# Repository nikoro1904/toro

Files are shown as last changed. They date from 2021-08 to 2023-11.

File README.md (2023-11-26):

# TORO

TORO is the name of my **T**ennis b**O**ll **RO**bot.

2023:
toro_112023
2021:
toro_082021

Some day in the future, TORO should be able to drive and navigate on a tennis court, search for tennis bolls, approach them, pick them up and eventually bring them back to me. It would also be nice to make TORO in a more generalistic matter so it can adapt or be adapted to different kind of bolls (such as golf bolls for example).

This repo contains general notes, electronic circuits, 3D parts and code of TORO. It is nowhere near being finished but will hopefully be some day. When this is the case, I might upload more detailed instructions on how to built TORO.

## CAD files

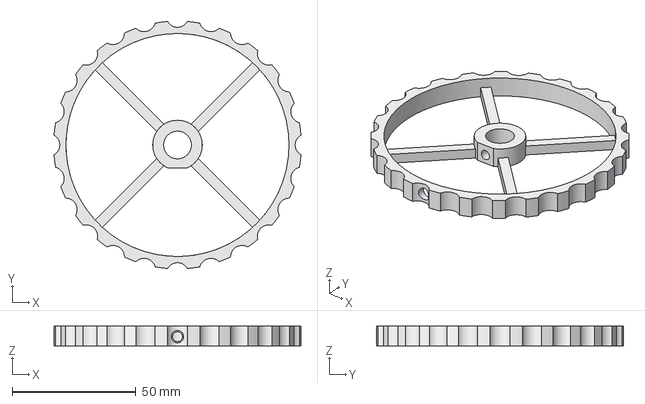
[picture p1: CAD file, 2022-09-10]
3d_parts/Rad_ringeinsatz.FCStd
99.7 x 99.7 x 8.00 mm

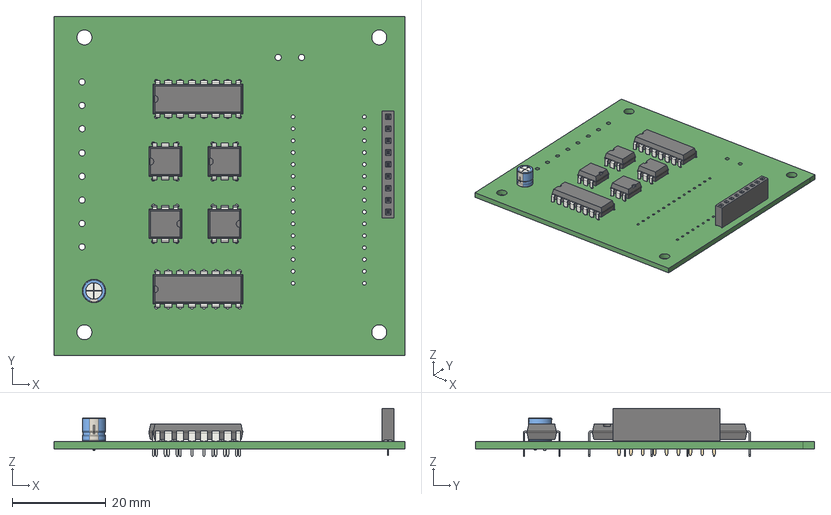
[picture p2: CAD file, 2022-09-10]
circuits/Toro_Stepper_Differential_Rev3/Toro_Stepper_Differential.step
75.0 x 72.5 x 10.3 mm

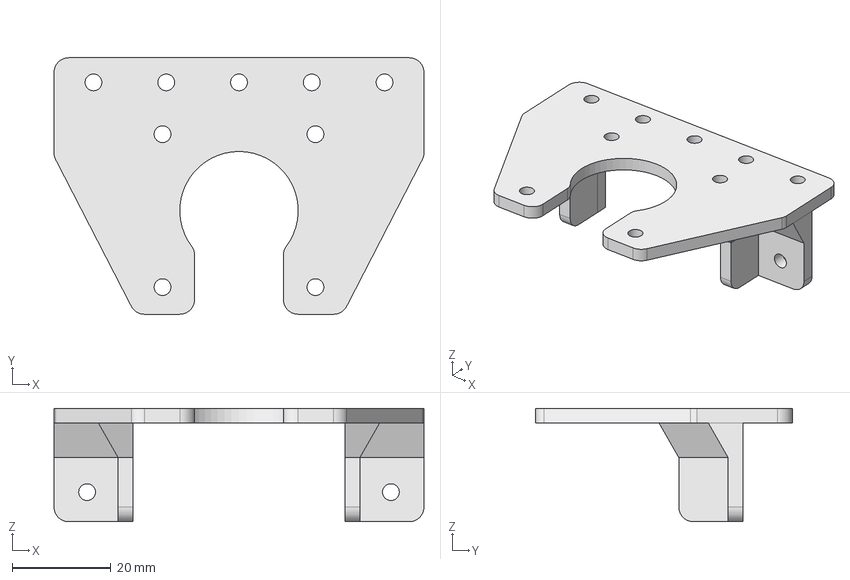
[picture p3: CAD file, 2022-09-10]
3d_parts/stepper_abdeckung.FCStd
75.0 x 52.0 x 23.0 mm

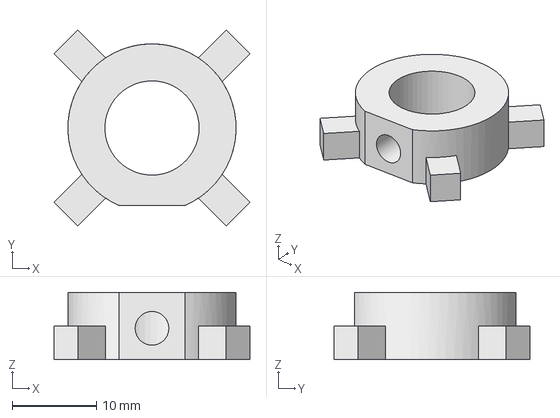
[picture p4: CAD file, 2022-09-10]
3d_parts/Rad_dummy_ringeinsatz.FCStd
23.3 x 23.3 x 8.00 mm

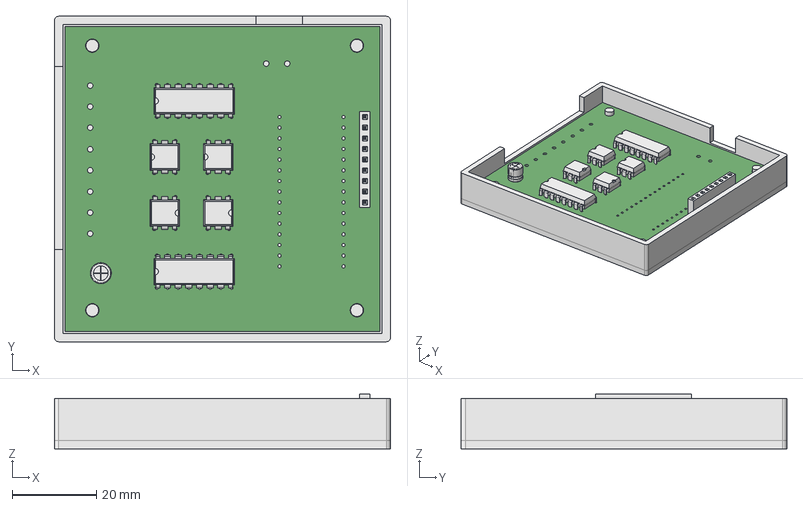
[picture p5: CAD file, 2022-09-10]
3d_parts/motor_platine_box.FCStd
80.0 x 77.5 x 13.1 mm

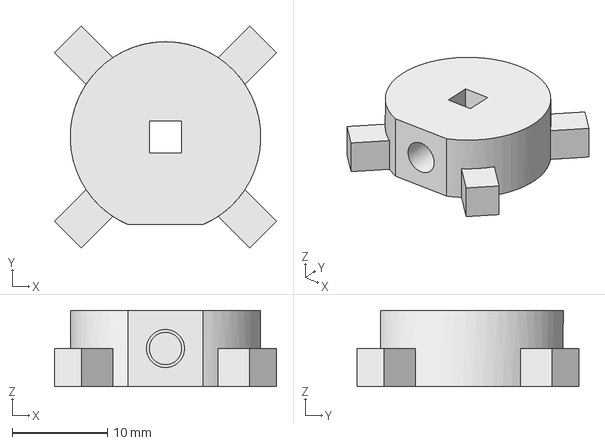
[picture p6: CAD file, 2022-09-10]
3d_parts/Rad_dummy_gewindeeinsatz.FCStd
23.3 x 23.3 x 8.00 mm

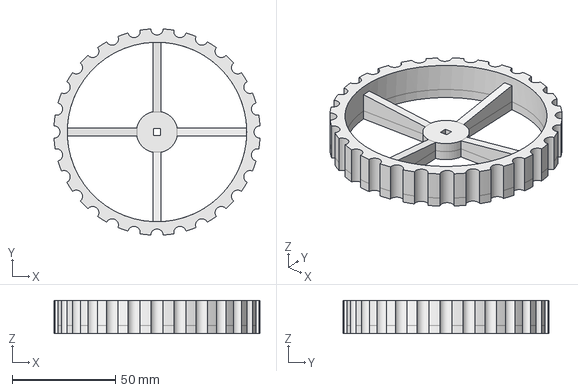
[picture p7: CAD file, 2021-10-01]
3d_parts/rad_breit_3,4.FCStd
99.8 x 99.8 x 16.0 mm

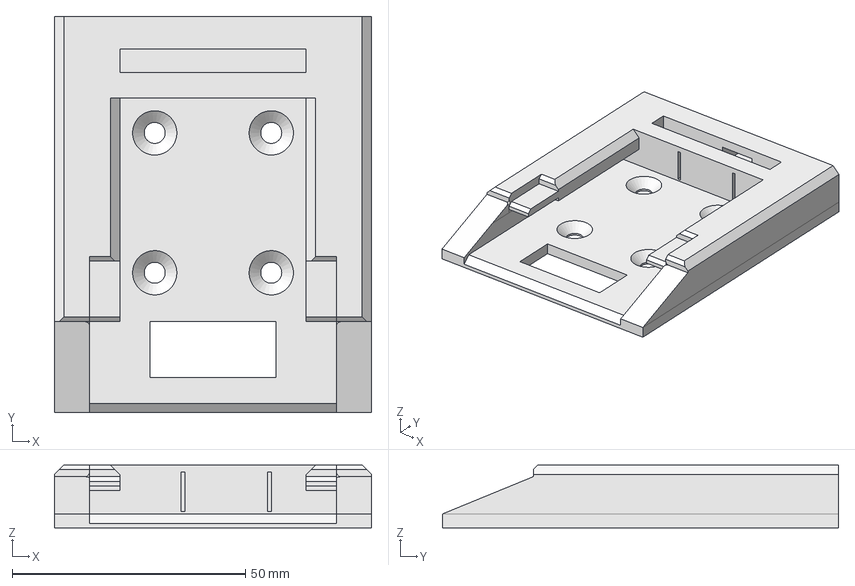
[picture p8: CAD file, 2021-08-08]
3d_parts/Akku_Aufnahme.FCStd
68.0 x 85.0 x 13.5 mm

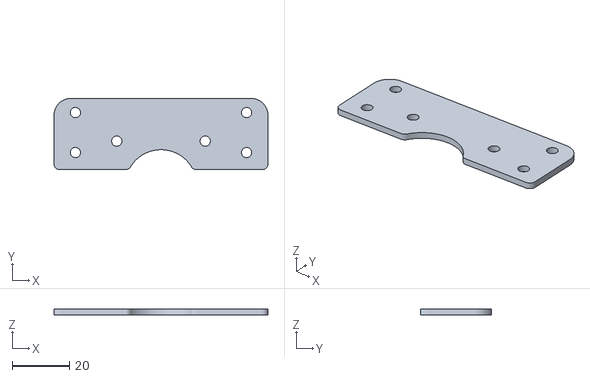
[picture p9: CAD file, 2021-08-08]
3d_parts/abdeckung_stepper_v2.stl
75.0 x 25.0 x 2.00

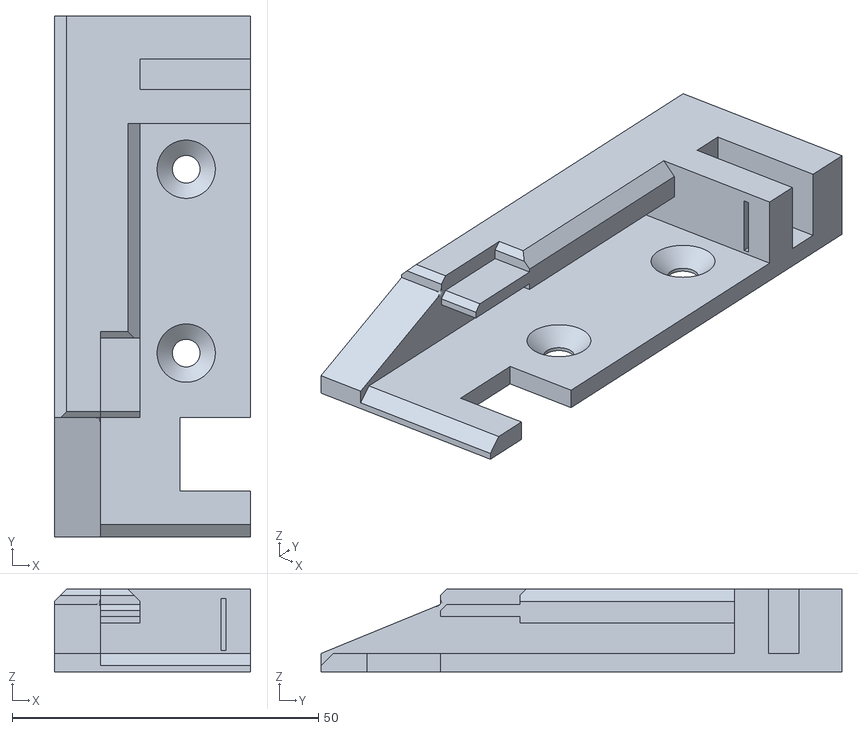
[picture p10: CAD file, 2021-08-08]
3d_parts/AA_kurz_v3.stl
32.0 x 85.0 x 13.5

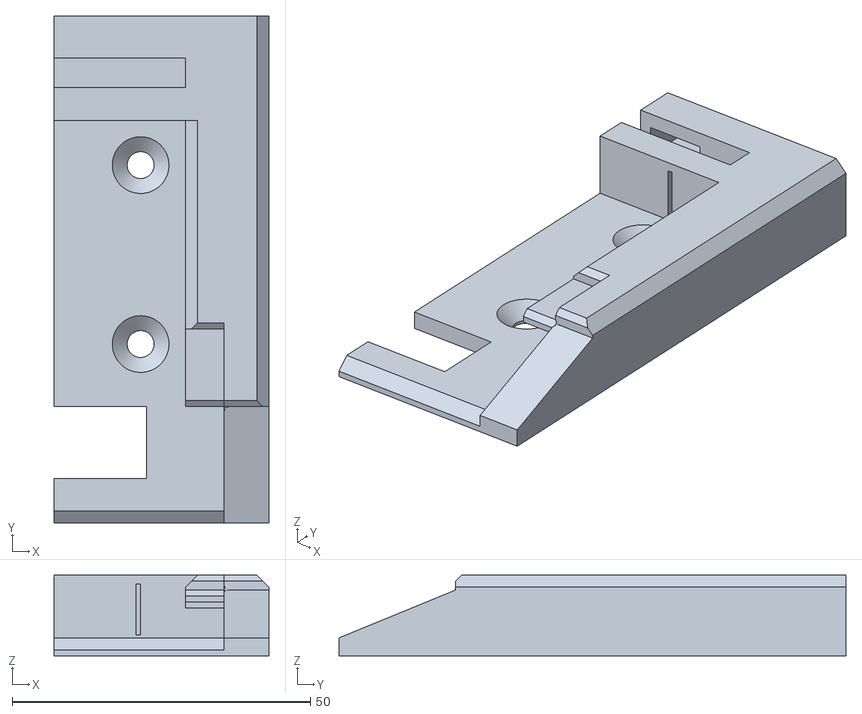
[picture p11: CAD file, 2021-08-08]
3d_parts/AA_lang_v3.stl
36.0 x 85.0 x 13.5

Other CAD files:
3d_parts/rad_komplett_3,4.FCStd
3d_parts/Rad_dummy_gewindeeinsatz.stl
3d_parts/Rad_ringeinsatz.stl
3d_parts/motor_platine_box.stl
3d_parts/rad_breit_3,4.stl
3d_parts/rad_komplett_3,4.stl

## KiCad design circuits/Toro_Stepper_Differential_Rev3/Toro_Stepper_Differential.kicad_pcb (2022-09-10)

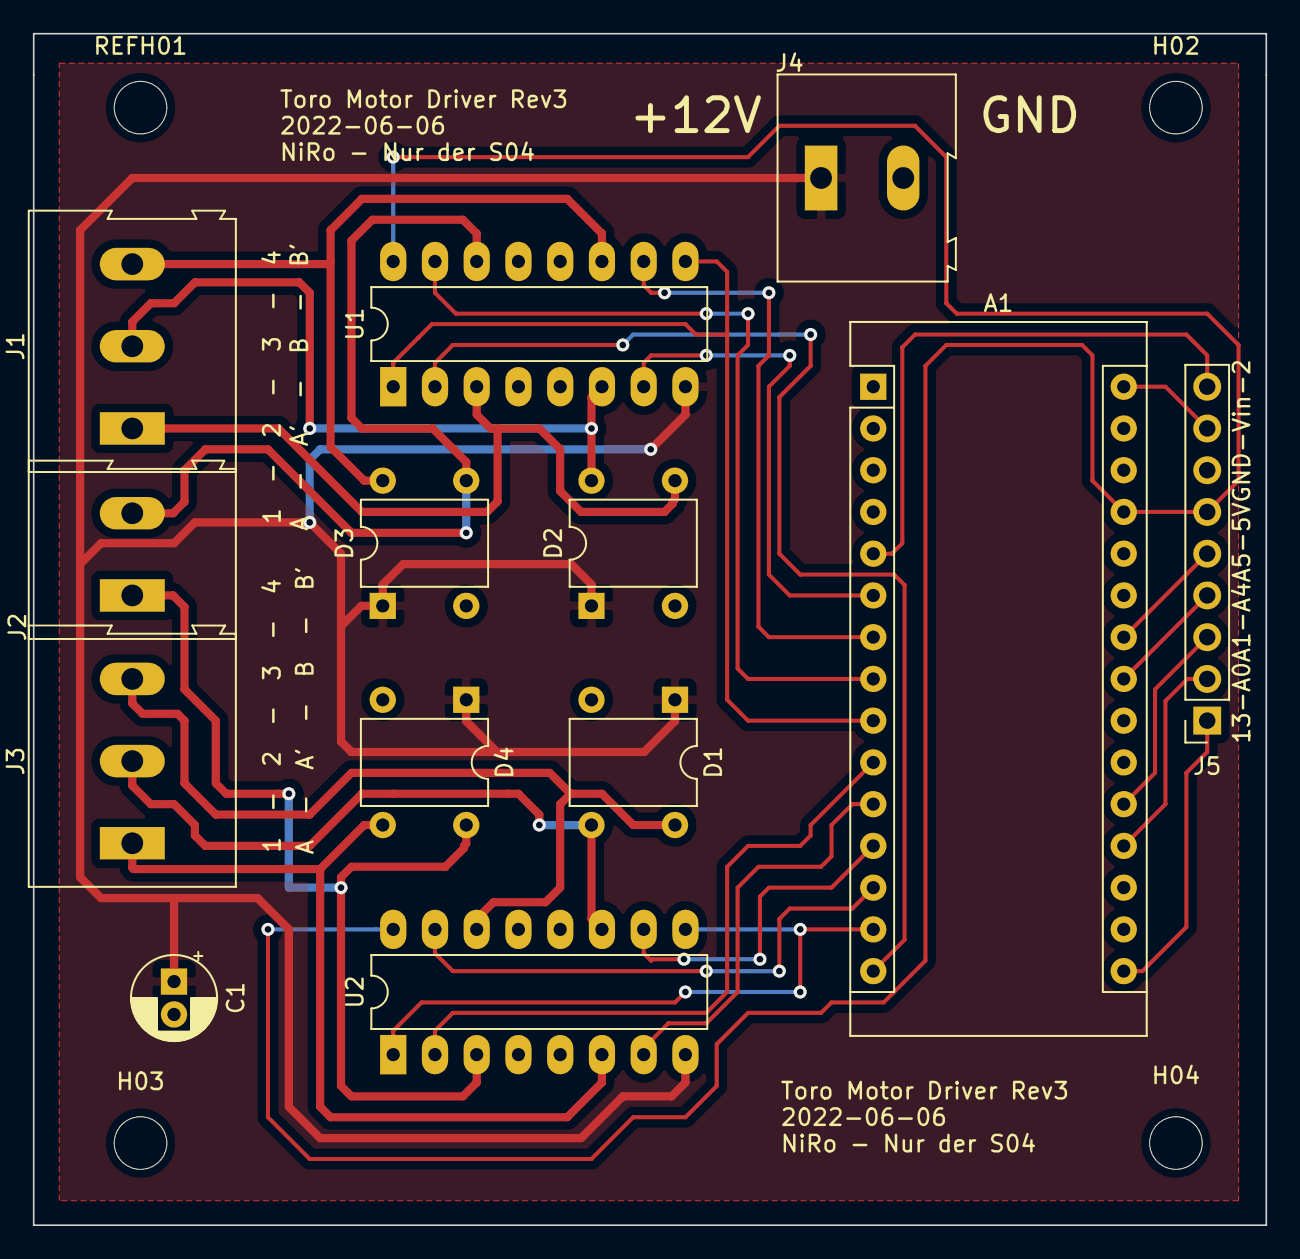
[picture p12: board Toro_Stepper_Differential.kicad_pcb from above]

Board: 2 copper layers, 75.0 x 72.5 mm, 17 parts (0 on the bottom side), 28 nets.

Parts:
A1: Arduino_Nano_v3.x; Arduino_Nano
C1: 220nF; CP_Radial_D5.0mm_P2.00mm
D1, D2, D3, D4: D_Bridge_+-AA; BridgeRectifier_+-AA
H02, H03, H04: MountingHole_3.2mm_M3_ISO14580
J1, J3: Screw_Terminal_01x03; TerminalBlock_Altech_AK300-3_P5.00mm
J2: Screw_Terminal_01x02; TerminalBlock_Altech_AK300-2_P5.00mm
J4: Screw_Terminal _01x02; TerminalBlock_Altech_AK300-2_P5.00mm
J5: Conn_01x09_Male; PinSocket_1x09_P2.54mm_Vertical
REFH01: MountingHole_3.2mm_M3_ISO14580
U1, U2: L293; DIP-16_W7.62mm_LongPads

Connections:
+10V: C1.1, D1.1, D2.1, D3.1, D4.1, J4.1, U1.8, U2.8
GND: A1.4, A1.29, C1.2, D1.2, D2.2, D3.2, D4.2, J4.2, J5.7, U1.4, U1.5, U1.12, U1.13, U2.4, U2.5, U2.12, U2.13
unnamed: A1.5, J5.9
unnamed: A1.6, U1.7
unnamed: A1.7, U1.10
unnamed: A1.8, U1.15
unnamed: A1.9, U1.1, U1.9
unnamed: A1.10, U2.2
unnamed: A1.11, U2.7
unnamed: A1.12, U2.10
unnamed: A1.13, U2.15
unnamed: A1.14, U2.1, U2.9
unnamed: A1.15, U1.2
unnamed: A1.16, J5.1
unnamed: A1.19, J5.2
unnamed: A1.20, J5.3
unnamed: A1.23, J5.4
unnamed: A1.24, J5.5
unnamed: A1.27, J5.6, U1.16, U2.16
unnamed: A1.30, J5.8
unnamed: D1.3, J3.2, U2.11
unnamed: D1.4, J3.3, U2.14
unnamed: D2.3, J1.1, U1.3
unnamed: D2.4, J1.2, U1.6
unnamed: D3.3, J2.2, U1.14
unnamed: D3.4, J1.3, U1.11
unnamed: D4.3, J3.1, U2.6
unnamed: D4.4, J2.1, U2.3

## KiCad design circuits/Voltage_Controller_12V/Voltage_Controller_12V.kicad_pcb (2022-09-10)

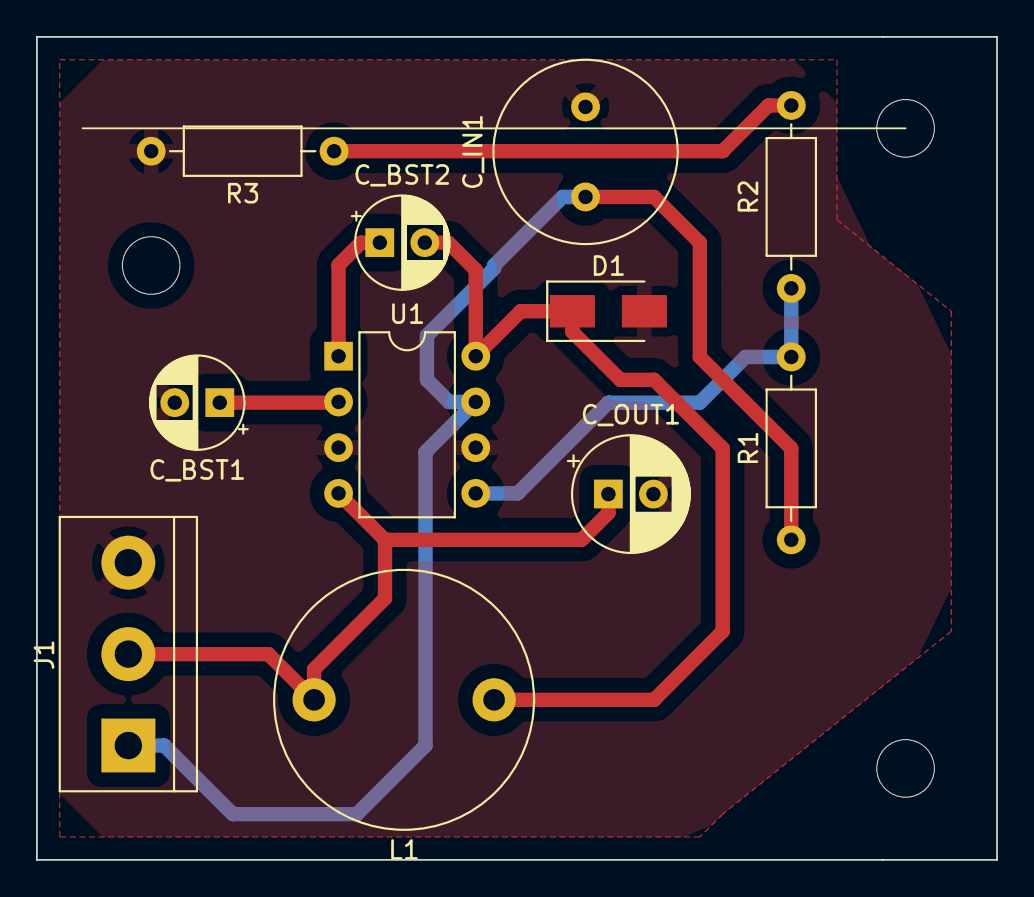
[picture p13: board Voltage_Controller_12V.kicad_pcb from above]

Board: 2 copper layers, 53.3 x 45.7 mm, 11 parts (0 on the bottom side), 8 nets.

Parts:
C_BST1, C_BST2: 0.1µF Tantal; CP_Radial_D5.0mm_P2.50mm
C_IN1: 220µF ELKO; C_Radial_D10.0mm_H16.0mm_P5.00mm
C_OUT1: 15µF Tantal; CP_Radial_D6.3mm_P2.50mm
D1: MBRA 340T3G ONS; D_SMA
J1: Screw_Terminal_01x03; TerminalBlock_bornier-3_P5.08mm
L1: 220µH; L_Radial_D14.2mm_P10.00mm_Neosid_SD14
R1: 1M; R_Axial_DIN0207_L6.3mm_D2.5mm_P10.16mm_Horizontal
R2: 100K; R_Axial_DIN0207_L6.3mm_D2.5mm_P10.16mm_Horizontal
R3: 47K; R_Axial_DIN0207_L6.3mm_D2.5mm_P10.16mm_Horizontal
U1: MAX5035CUPA; DIP-8_W7.62mm

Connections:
+12V: C_OUT1.1, J1.2, L1.2, U1.4
GND: C_BST1.2, C_IN1.2, C_OUT1.2, D1.2, J1.3, R3.2, U1.3, U1.6
unnamed: C_BST1.1, U1.2
unnamed: C_BST2.1, U1.1
unnamed: C_BST2.2, D1.1, L1.1, U1.8
unnamed: R1.2, R2.1, U1.5
unnamed: R2.2, R3.1
Vdrive: C_IN1.1, J1.1, R1.1, U1.7

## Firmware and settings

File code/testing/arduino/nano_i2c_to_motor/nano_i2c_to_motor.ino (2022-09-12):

/*
 * Niko Rosberg, TORO Project, 27-Sept-2021
 * Code for readout of I2C values (from ESP32)
 * and sending of motor commands to the L293 board.
 * 
 */

// I2C pins
#define SDA A4
#define SCL A5

// L293 pins
#define EN_R 11
#define EN_L 6

//                   {A,B,A',B'}
const int PIN_R[4] = {7,9,8,10};
const int PIN_L[4] = {12,4,3,5}; //{11,8,10,7};

//Pin p:                  p =  1A   2B    3A'  4B'      // Schritt s:
const int FULLSTEP[4][4] = { {HIGH, HIGH, LOW, LOW },   // s = 0 / U
                             {LOW, HIGH, HIGH, LOW },   // s = 1 / V
                             {LOW, LOW, HIGH, HIGH },   // s = 2 / W
                             {HIGH, LOW, LOW, HIGH } }; // s = 3 / X

volatile uint8_t dir = 0xFF;
volatile uint8_t interval = 10;
int distance = 10;
int rotation = 10;

#include <Wire.h>
#define I2C_ADDRESS 0x04

void setup() {
  for (int i=3; i<=12; i++) {
    pinMode(i, OUTPUT);
  }
  both_motors_on();

  Wire.begin(I2C_ADDRESS);
  Wire.onReceive(readI2Cinput);
}

void loop() {
  // put your main code here, to run repeatedly:


  switch (dir) {
    case 0x00:    // drive backwards
      both_motors_on();
      drive_backwards(distance, interval);
      break;
    case 0x01:                                // turn front left
      both_motors_on();
      turn_front_left(rotation, interval);
      break;
    case 0x02:                                // turn front right
      both_motors_on();
      turn_front_right(rotation, interval);
      break;
    case 0x03:                                // drive forward
      both_motors_on();
      drive_forward(distance, interval);
      break;
    case 0x04:                                // rotate left
      both_motors_on();
      rotate_left(rotation, interval);
      break;
    case 0x05:// rotate right
      both_motors_on();
      rotate_right(rotation, interval);
      break;
    case 0x06:                                // drive fast forward
      both_motors_on();
      drive_forward(distance, 2*interval/3);
      break;
    case 0x07:                                // turn back left
      both_motors_on();
      turn_back_left(rotation, interval);
      break;
    case 0x08:                                // turn back right
      both_motors_on();
      turn_back_right(rotation, interval);
      break;
    case 0x10:
      both_motors_on();
      drive_backwards(distance, 2*interval/3);
      break;
    case 0x11:
      both_motors_on();
      rotate_left(rotation, interval);
    case 0xa0:
      both_motors_off();
      interval = 3;
      break;
    case 0xa1:
      both_motors_off();
      interval = 5;
      break;
    case 0xa2:
      both_motors_off();
      interval = 10;
      break;
    case 0xa3:
      both_motors_off();
      interval = 15;
      break;
    case 0xa4:
      both_motors_off();
      interval = 20;
      break;
    case 0xa5:
      both_motors_off();
      interval = 25;
    case 0xfd:  // msg 0xfd is reserved for esp32-master communication
      break;
    case 0xfe:  // msg 0xfe is reserved for esp32-master communication
      break;
    case 0xff:
      both_motors_off();                      // off
    default:
      both_motors_off();                      // off
  }
}

void readI2Cinput(int howMany) {
  while(Wire.available() > 0) {
    dir = Wire.read();
  }
}

void turn_back_left(int steps, int my_pause) {
  for (int i=0; i<steps; i++) {
    for (int s = 0; s < 4; s++) {
        for (int p = 0; p < 4; p++) {
          digitalWrite(PIN_L[p], FULLSTEP[3-s][p]); // L backwards
          digitalWrite(PIN_R[p], LOW); // R stands
        }
      delay(my_pause);
    }
  }
}

void turn_back_right(int steps, int my_pause) {
  for (int i=0; i<steps; i++) {
    for (int s = 0; s < 4; s++) {
        for (int p = 0; p < 4; p++) {
          digitalWrite(PIN_L[p], LOW); // L forward
          digitalWrite(PIN_R[p], FULLSTEP[s][p]); // R stands
        }
      delay(my_pause);
    }
  }
}

void turn_front_left(int steps, int my_pause) {
  for (int i=0; i<steps; i++) {
    for (int s = 0; s < 4; s++) {
        for (int p = 0; p < 4; p++) {
          digitalWrite(PIN_L[p], LOW); // L stands
          digitalWrite(PIN_R[p], FULLSTEP[3-s][p]); // R forward
        }
      delay(my_pause);
    }
  }
}

void turn_front_right(int steps, int my_pause) {
  for (int i=0; i<steps; i++) {
    for (int s = 0; s < 4; s++) {
        for (int p = 0; p < 4; p++) {
          digitalWrite(PIN_L[p], FULLSTEP[s][p]); // L forward
          digitalWrite(PIN_R[p], LOW); // R stands
        }
      delay(my_pause);
    }
  }
}

void rotate_left(int steps, int my_pause) {
  for (int i=0; i<steps; i++) {
    for (int s = 0; s < 4; s++) {
        for (int p = 0; p < 4; p++) {
          digitalWrite(PIN_L[p], FULLSTEP[3-s][p]); // L backwards
          digitalWrite(PIN_R[p], FULLSTEP[3-s][p]); // R forward
        }
      delay(my_pause);
    }
  }
}

void rotate_right(int steps, int my_pause) {
  for (int i=0; i<steps; i++) {
    for (int s = 0; s < 4; s++) {
        for (int p = 0; p < 4; p++) {
          digitalWrite(PIN_L[p], FULLSTEP[s][p]); // L forward
          digitalWrite(PIN_R[p], FULLSTEP[s][p]); // R backward
        }
      delay(my_pause);
    }
  }
}
void drive_forward(int steps, int my_pause) {
  for (int i=0; i<steps; i++) {
    for (int s = 0; s < 4; s++) {
      for (int p = 0; p < 4; p++) {
        digitalWrite(PIN_L[p], FULLSTEP[s][p]); // L forward
        digitalWrite(PIN_R[p], FULLSTEP[3-s][p]); // R forward
        }
      delay(my_pause);
    }
  }
}

void drive_backwards(int steps, int my_pause) {
  for (int i=0; i<steps; i++) {
      for (int s = 0; s < 4; s++) {
        for (int p = 0; p < 4; p++) {
          digitalWrite(PIN_L[p], FULLSTEP[3-s][p]); // L backwards
          digitalWrite(PIN_R[p], FULLSTEP[s][p]);  // R backwards
          }
      delay(my_pause);
    }
  }
}

void both_motors_on() {
  digitalWrite(EN_L, HIGH);
  digitalWrite(EN_R, HIGH);
}

void both_motors_off() {
  for (int s = 0; s < 4; s++) {
    for (int p = 0; p < 4; p++) {
      digitalWrite(PIN_L[p], LOW); // L backwards
      digitalWrite(PIN_R[p], LOW);  // R backwards
    }
  }
  digitalWrite(EN_L, LOW);
  digitalWrite(EN_R, LOW);
}

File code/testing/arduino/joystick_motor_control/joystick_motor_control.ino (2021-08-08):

/* Niko Rosberg, TORO Project, 13-05-2021
*  Code for readout of joystick and motor control
*  use L293B board
*/
#define FB_PIN A5
#define LR_PIN A4

#define EN_R 3
#define EN_L 5

#define IN_R1 7
#define IN_R2 2
#define IN_L1 4
#define IN_L2 6

void setup() {
  // put your setup code here, to run once:
  Serial.begin(115200);

  for (int i=2; i<7; i++) {
    pinMode(i, OUTPUT);
  }
}

void loop() {
  // put your main code here, to run repeatedly:

  // read analog values (0...1023)
  int senseFB = analogRead(FB_PIN);
  int senseLR = analogRead(LR_PIN);

  // calculate normalized output values (-5...5)
  int normFB = map(senseFB, 0, 1023, -5, 5);
  int normLR = map(senseLR, 0, 1023, -5, 5);

  // calc motor control values
  int motorControlR = normFB + normLR;
  int motorControlL = normFB - normLR;

  // calc PWM values
  int signedPwmR = map(motorControlR, -10, 10, -255, 255);
  int signedPwmL = map(motorControlL, -10, 10, -255, 255);

  // get abs values
  int pwmR = abs(signedPwmR);
  int pwmL = abs(signedPwmL);

  // get signs
  int dirR = getIntSign(signedPwmR);
  int dirL = getIntSign(signedPwmL);

  // set input/direction pins
  setInputPins(dirR, IN_R1, IN_R2);
  setInputPins(dirL, IN_L1, IN_L2);

  // set enable/strength pins
  analogWrite(EN_R, pwmR);
  analogWrite(EN_L, pwmL);

  Serial.print(motorControlR);
  Serial.print("  ");
  Serial.println(motorControlL);
  delay(100);
}

int getIntSign(int integer) {
  if (integer >> 15) {
    return 1;
  } else {
      return -1;
  }
}

void setInputPins(int direction, int in1, int in2) {
  if (direction > 0) {
    digitalWrite(in1, HIGH);
    digitalWrite(in2, LOW);
  } else {
    digitalWrite(in1, LOW);
    digitalWrite(in2, HIGH);
  }
}

void setEnablePin(int strength, int en) {
  int pwmValue = map(strength, 0, 5, 0, 255);
  analogWrite(en, pwmValue);
}

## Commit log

2021-08-08 added old files
    [AA_kurz_v3.stl, AA_lang_v3.stl, Akku_Aufnahme.FCStd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]
2021-08-28 added new circuit
    [Voltage_Controller_12V.kicad_pcb, Voltage_Controller_12V.sch]
2021-10-01 made bluetooth connection work
    [Toro_Stepper_Differential.sch, rad_breit_3,4.FCStd, rad_breit_3,4.stl]
2022-06-04 added rev2 and rev3 with diodes and bridge rectifier, respectively
    [Toro_Stepper_Differential.kicad_pcb, Toro_Stepper_Differential.sch]
2022-07-21 stepper test
2022-07-21 fixed oscillations for turn_right
    [nano_i2c_to_motor.ino]
2022-07-21 added excel for hardware connections
    [verbindungen.ods]
2022-08-29 created venv for opencv dev
    [pyvenv.cfg]
2022-09-10 removed venv from git tracking
    [pyvenv.cfg]
2022-09-12 added and removed changes for i2c msg handling
2023-11-26 added serial init handshake for motor driver module
2023-11-26 first steps for remote control of motors
